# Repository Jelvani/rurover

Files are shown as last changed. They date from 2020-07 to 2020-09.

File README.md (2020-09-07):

# Rutgers Rover (RURover) User Guide (Under Develpoment)

RURover is an unmaned-ground-vehicke (UGV) based on the [Traxxas X-Maxx 8s](https://traxxas.com/products/landing/x-maxx/), that has been modified with the addition of wheel encoders, steering sensor, and an on-board embedded system.

## Hardware
***
A list of all additional hardware added to RURover can be found below:
- Sensors
    - [Wheel encoders (X4)](https://www.usdigital.com/products/encoders/incremental/shaft/S4T)
    - [Steering angle encoder](https://www.usdigital.com/products/encoders/absolute/magnetic/MA3)
    - [Inertial Measurement Unit (IMU)](https://www.adafruit.com/product/2472)
- Embedded System
    - [System on module, NVIDIA Jetson TX2](https://developer.nvidia.com/embedded/jetson-tx2-developer-kit)
    - [Jetson TX2 custom carrier board](https://www.uta.edu/utari/research/robotics/airborne/tutorials.php#TX2version2)
    - [Teensy 4.0 microcontroller](https://www.pjrc.com/store/teensy40.html)
- Batteries
    - [6500 mAh 4s LiPo (X2)](https://www.amazon.com/Youme-Battery-6500mAh-Traxxas-%EF%BC%8CHelicopter%EF%BC%8CAirplane/dp/B07PD2CNQM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)

## Robot Operating System (ROS) Specifications
***

## Connecting to the platform
***
1. Choose the wifi network with SSID `rurover` and password is `rurover-ram-lab`.
2. SSH into the TX2 with `ssh rurover@10.42.0.1` and password is `12`.

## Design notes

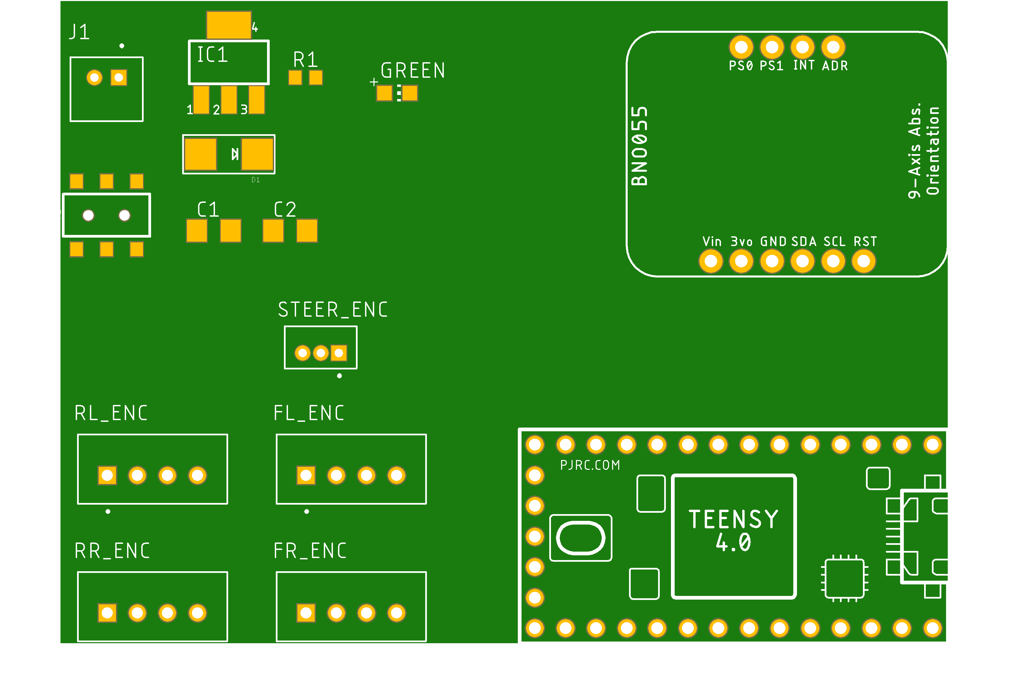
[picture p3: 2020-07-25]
pcb_boards/pcb.png

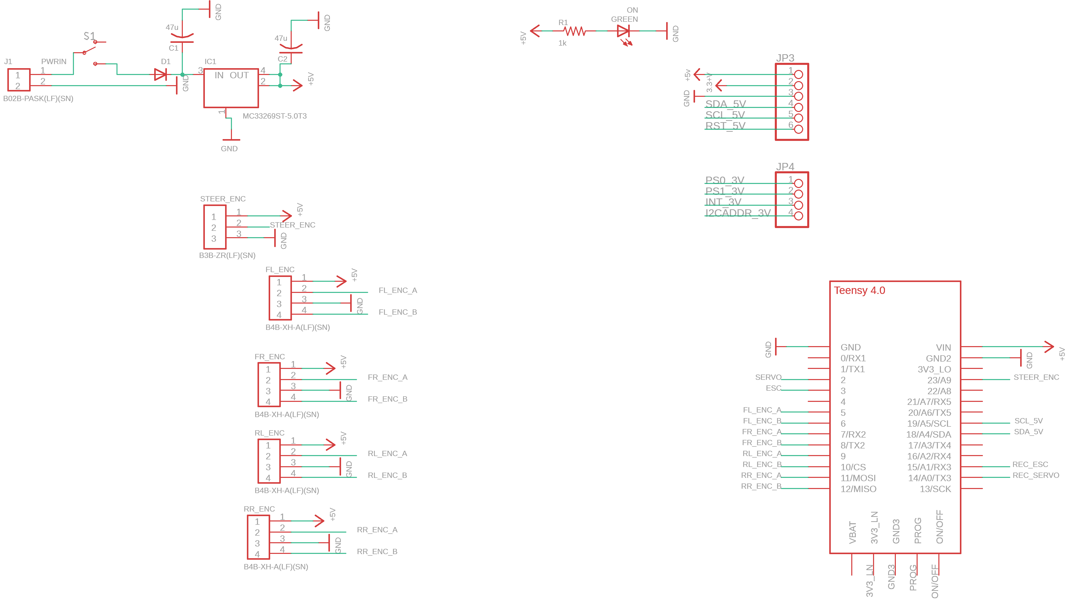
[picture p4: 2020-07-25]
pcb_boards/circuit.png

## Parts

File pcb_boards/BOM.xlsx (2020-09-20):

Part | Value | Device | Package | Description | MF | MPN | MOUNT TYPE
C1 | 0.1uF | C-USC1206 | 1206 | Multilayer Ceramic Capacitors MLCC - SMD/SMT 50V 0.1uF X7R AUTO 5mm Flex VW 80808 | KEMET | C1206X104K5RAC3316 | SMD/SMT
C2 | 10uF | C-USC1206 | 1206 | Multilayer Ceramic Capacitors MLCC - SMD/SMT 16V 10uF Y5V 1206 -20/80% | KEMET | C1206C106Z4VACTU | SMD/SMT
D1 |  | DIODESMA | SMA (DO-214AC) | Schottky Diodes & Rectifiers 40 Volt 1.0 Amp 40 Amp IFSM | Vishay Semiconductors | SS14-E3/5AT | SMD/SMT
ESC |  | JST-XH-02-PIN-LONG-PAD | 2POS | CONN HEADER VERT 2POS 2.5MM | JST Sales America Inc | B2B-XH-A(LF)(SN) | Through Hole
FL_ENC |  | JST-XH-04-PIN-LONG-PAD | 4POS | CONN HEADER VERT 4POS 2.5MM | JST Sales America Inc | B4B-XH-A(LF)(SN) | Through Hole
FR_ENC |  | JST-XH-04-PIN-LONG-PAD | 4POS | CONN HEADER VERT 4POS 2.5MM | JST Sales America Inc | B4B-XH-A(LF)(SN) | Through Hole
GREEN |  | LEDCHIP-LED0805 | 0805 | LED GREEN DIFFUSED 0805 SMD | OSRAM Opto Semiconductors Inc. | LG R971-KN-1 | SMD
IC1 | LM2937IMP-5.0 | LM2937IMP-5.0 | SOT-223-4 | LDO Voltage Regulators 500 MA LDO REG | Texas Instruments | LM2937IMP-5.0/NOPB | SMD
PWR_IN |  | JST-XH-02-PIN-LONG-PAD | 2POS | CONN HEADER VERT 2POS 2.5MM | JST Sales America Inc | B2B-XH-A-M(LF)(SN) | Through Hole
R1 | 1kOhms | R-US_R0603 | 0603 | Thick Film Resistors - SMD AEC-Q200 | Panasonic | ERJ-UP3D1001V | SMD/SMT
RECIEVER |  | JST-XH-03-PIN-LONG-PAD | 3POS | CONN HEADER VERT 3POS 2.5MM | JST Sales America Inc | B3B-XH-A(LF)(SN) | Through Hole
RL_ENC |  | JST-XH-04-PIN-LONG-PAD | 4POS | CONN HEADER VERT 4POS 2.5MM | JST Sales America Inc | B4B-XH-A(LF)(SN) | Through Hole
RR_ENC |  | JST-XH-04-PIN-LONG-PAD | 4POS | CONN HEADER VERT 4POS 2.5MM | JST Sales America Inc | B4B-XH-A(LF)(SN) | Through Hole
S1 |  | SWITCH-SPDT-SMD-AYZ0202 | DPDT | SWITCH SLIDE DPDT 100MA 12V | C&K | AYZ0202AGRLC | SMD
SERVO |  | JST-XH-02-PIN-LONG-PAD | 2POS | CONN HEADER VERT 2POS 2.5MM | JST Sales America Inc | B2B-XH-A(LF)(SN) | Through Hole
STEER_ENC |  | JST-XH-03-PIN-LONG-PAD | 3POS | CONN HEADER VERT 3POS 2.5MM | JST Sales America Inc | B3B-XH-A(LF)(SN) | Through Hole

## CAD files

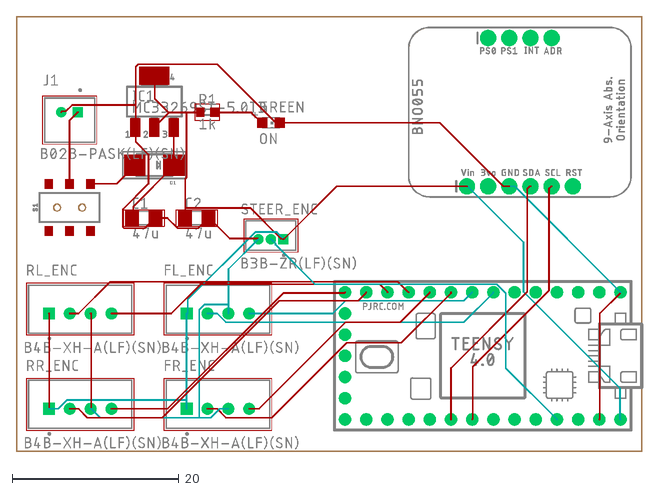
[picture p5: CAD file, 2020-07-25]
pcb_boards/rover.dxf
75.2 x 52.2

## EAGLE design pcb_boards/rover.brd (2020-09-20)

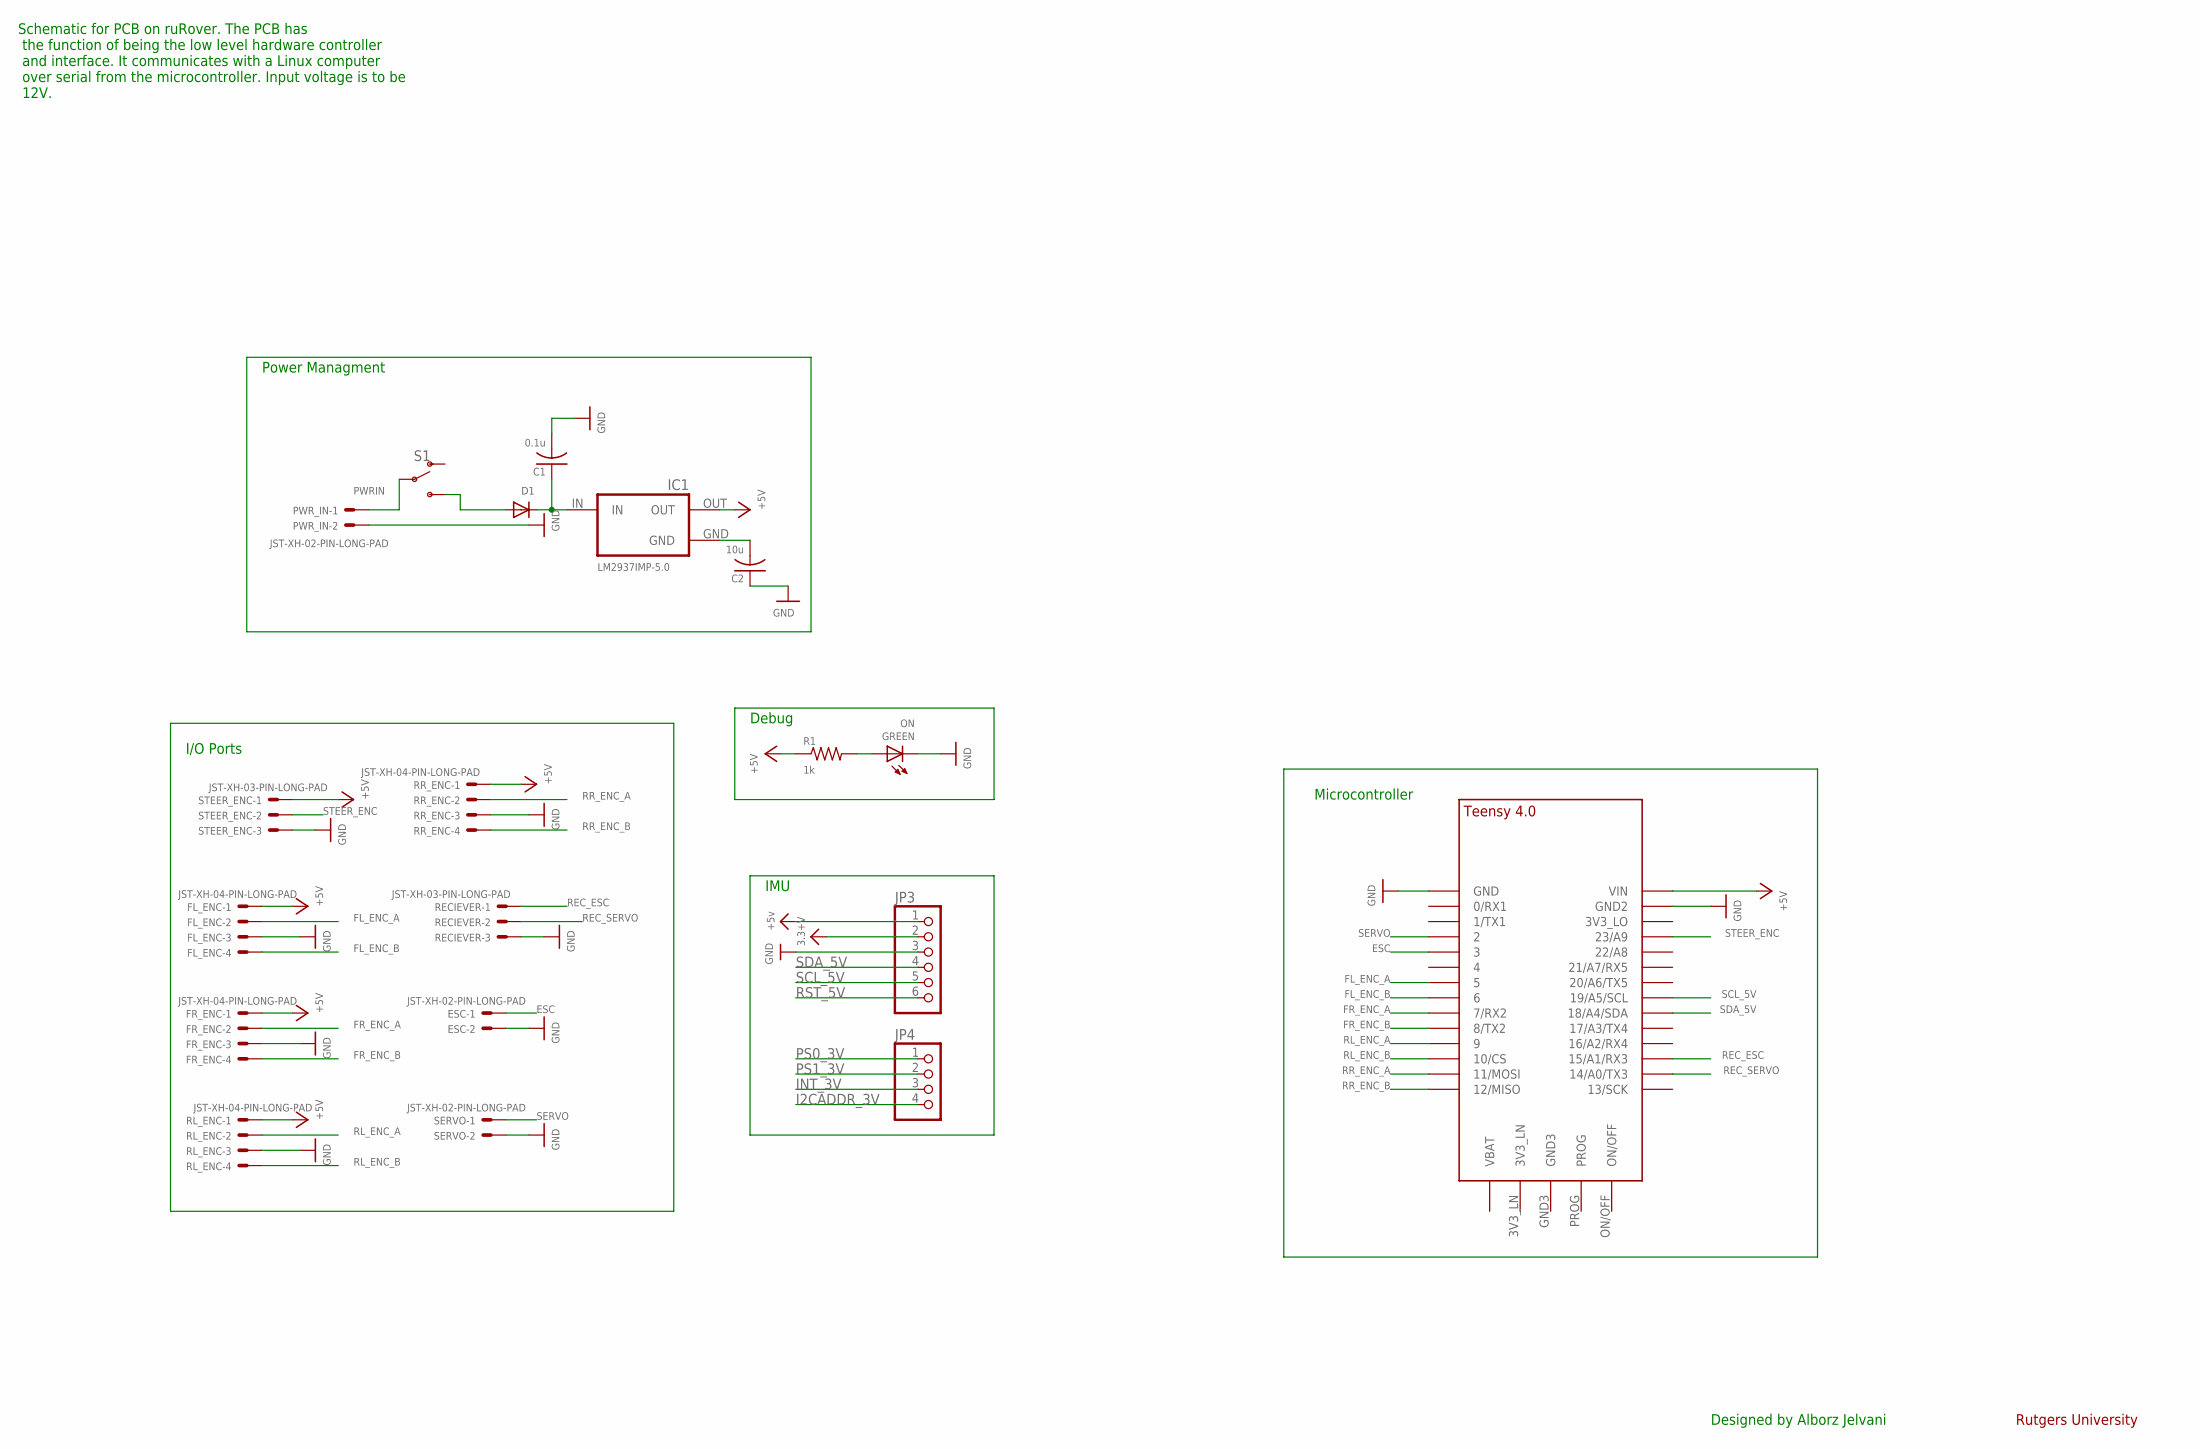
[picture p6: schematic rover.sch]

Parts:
C1: 0.1u; C1206
C2: 10u; C1206
D1: DIODESMA; SMADIODE
ESC: JST-XH-02-PIN-LONG-PAD; JST-XH-02-PACKAGE-LONG-PAD
FL_ENC: JST-XH-04-PIN-LONG-PAD; JST-XH-04-PACKAGE-LONG-PAD
FR_ENC: JST-XH-04-PIN-LONG-PAD; JST-XH-04-PACKAGE-LONG-PAD
GREEN: ON; CHIP-LED0805
IC1: LM2937IMP-5.0; SOT223
JP3: HEADER-1X676MIL; 1X06_ROUND_76
JP4: HEADER-1X476MIL; 1X04_ROUND_76
PWR_IN: JST-XH-02-PIN-LONG-PAD; JST-XH-02-PACKAGE-LONG-PAD
R1: 1k; R0603
RECIEVER: JST-XH-03-PIN-LONG-PAD; JST-XH-03-PACKAGE-LONG-PAD
RL_ENC: JST-XH-04-PIN-LONG-PAD; JST-XH-04-PACKAGE-LONG-PAD
RR_ENC: JST-XH-04-PIN-LONG-PAD; JST-XH-04-PACKAGE-LONG-PAD
S1: SWITCH-SPDT-SMD-AYZ0202; SWITCH_DPDT_SMD_AYZ0202
SERVO: JST-XH-02-PIN-LONG-PAD; JST-XH-02-PACKAGE-LONG-PAD
STEER_ENC: JST-XH-03-PIN-LONG-PAD; JST-XH-03-PACKAGE-LONG-PAD
U$5: TEENSY_4.0-BASIC

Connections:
+3.3V: JP3.2
+5V: FL_ENC.1, FR_ENC.1, IC1.OUT, JP3.1, R1.1, RL_ENC.1, RR_ENC.1, STEER_ENC.1, U$5.VIN
ESC: ESC.1, U$5.3/CANTX (3)
FL_ENC_A: FL_ENC.2, U$5.5
FL_ENC_B: FL_ENC.4, U$5.6
FR_ENC_A: FR_ENC.2, U$5.7 (7/RX2)
FR_ENC_B: FR_ENC.4, U$5.8 (8/TX2)
GND: C1.2, C2.1, ESC.2, FL_ENC.3, FR_ENC.3, GREEN.C, IC1.GND@ (GND), JP3.3, PWR_IN.2, RECIEVER.3, RL_ENC.3, RR_ENC.3, SERVO.2, STEER_ENC.3, U$5.GND, U$5.GND2
I2CADDR_3V: JP4.4
INT_3V: JP4.3
unnamed: GREEN.A, R1.2
unnamed: C1.1, D1.C, IC1.IN
unnamed: D1.A, S1.3 (S)
unnamed: C2.2, IC1.GND
PS0_3V: JP4.1
PS1_3V: JP4.2
PWRIN: PWR_IN.1, S1.2
REC_ESC: RECIEVER.1, U$5.15/A1 (15/A1/RX3)
REC_SERVO: RECIEVER.2, U$5.14/A0 (14/A0/TX3)
RL_ENC_A: RL_ENC.2, U$5.9/CS (9)
RL_ENC_B: RL_ENC.4, U$5.10/CS
RR_ENC_A: RR_ENC.2, U$5.11/MOSI
RR_ENC_B: RR_ENC.4, U$5.12/MISO
RST_5V: JP3.6
SCL_5V: JP3.5, U$5.19/A5/SCL
SDA_5V: JP3.4, U$5.18/A4/SDA
SERVO: SERVO.1, U$5.2
STEER_ENC: STEER_ENC.2, U$5.23/A9

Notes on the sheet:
Rutgers University
Power Managment
I/O Ports
Debug
IMU
Microcontroller
Schematic for PCB on ruRover. The PCB has the function of being the low level hardware controller and interface. It communicates with a Linux computer over serial from the microcontroller. Input voltage is to be 12V.
Designed by Alborz Jelvani

Board: 2 copper layers, 23 parts (0 on the bottom side), 22 nets, no tracks yet.

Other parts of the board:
U$4, U$6, U$7, U$8: 3,6

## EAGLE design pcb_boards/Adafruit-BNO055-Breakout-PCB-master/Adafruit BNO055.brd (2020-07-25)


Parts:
C1, C2: 22pF; 0805-NO
C3: 0.1uF; 0805-NO
C4: 0.1uF; 0805_10MGAP
C5: 10uF; 0805-NO
C6: 10uF; 0805_10MGAP
D1: 1n4148; SOD-323
FID1, FID2: FIDUCIAL""; FIDUCIAL_1MM
JP1: HEADER-1X676MIL; 1X06_ROUND_76
JP2: HEADER-1X476MIL; 1X04_ROUND_76
Q1, Q2: BSS138; SOT23-WIDE
R3, R4, R5, R6, R7, R10: 10K; 0805-NO
R8, R9: 10K; _0805MP
U1: MIC5225-3.3; SOT23-5
U$2: BNO055
U$29, U$30, U$31, U$32: MOUNTINGHOLE2.5_THICK; MOUNTINGHOLE_2.5_PLATED_THICK
Y1: 32.768kHz; CRYSTAL_8X3.8

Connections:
3.3V: C4.2, C6.1, JP1.2, Q1.1 (G), Q2.1 (G), R6.2, R7.2, R10.2, U1.5 (OUT), U$2.3 (VDD), U$2.4 (NBOOT_LOAD_PIN), U$2.28 (VDDIO)
5.0V: C5.1, JP1.1, R8.2, R9.2, U1.1 (IN), U1.3 (EN)
GND: C1.1, C2.1, C3.1, C4.1, C5.2, C6.2, JP1.3, R3.2, R4.2, R5.2, U1.2 (GND), U$2.2 (GND), U$2.10 (PIN10(GND)), U$2.15 (PIN15(GND)), U$2.16 (PIN16(GND)), U$2.18 (COM2(GND)), U$2.25 (GND)
I2CADDR_3V: JP2.4, R5.1, U$2.17 (COM3/I2C_ADDR)
INT_3V: JP2.3, U$2.14 (INT)
unnamed: C1.2, U$2.27 (XIN32), Y1.P$4 (2)
unnamed: C2.2, U$2.26 (XOUT32), Y1.P$1 (1)
unnamed: C3.2, U$2.9 (CAP)
NRESET_3V: D1.A, R10.1, U$2.11 (NRESET)
PS0_3V: JP2.1, R3.1, U$2.6 (PS0)
PS1_3V: JP2.2, R4.1, U$2.5 (PS1)
RST_5V: D1.C, JP1.6
SCL_3V: Q2.2 (S), R7.1, U$2.19 (COM1/SCL/RX)
SCL_5V: JP1.5, Q2.3 (D), R9.1
SDA_3V: Q1.2 (S), R6.1, U$2.20 (COM0/SDA/TX)
SDA_5V: JP1.4, Q1.3 (D), R8.1



Board: 2 copper layers, 26.7 x 20.3 mm, 31 parts (2 on the bottom side), 16 nets.

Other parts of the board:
U$3: PCBFEAT-REV-040
U$28: ADAFRUIT_TEXT_20MM
U$33: ADAFRUIT_2.5MM

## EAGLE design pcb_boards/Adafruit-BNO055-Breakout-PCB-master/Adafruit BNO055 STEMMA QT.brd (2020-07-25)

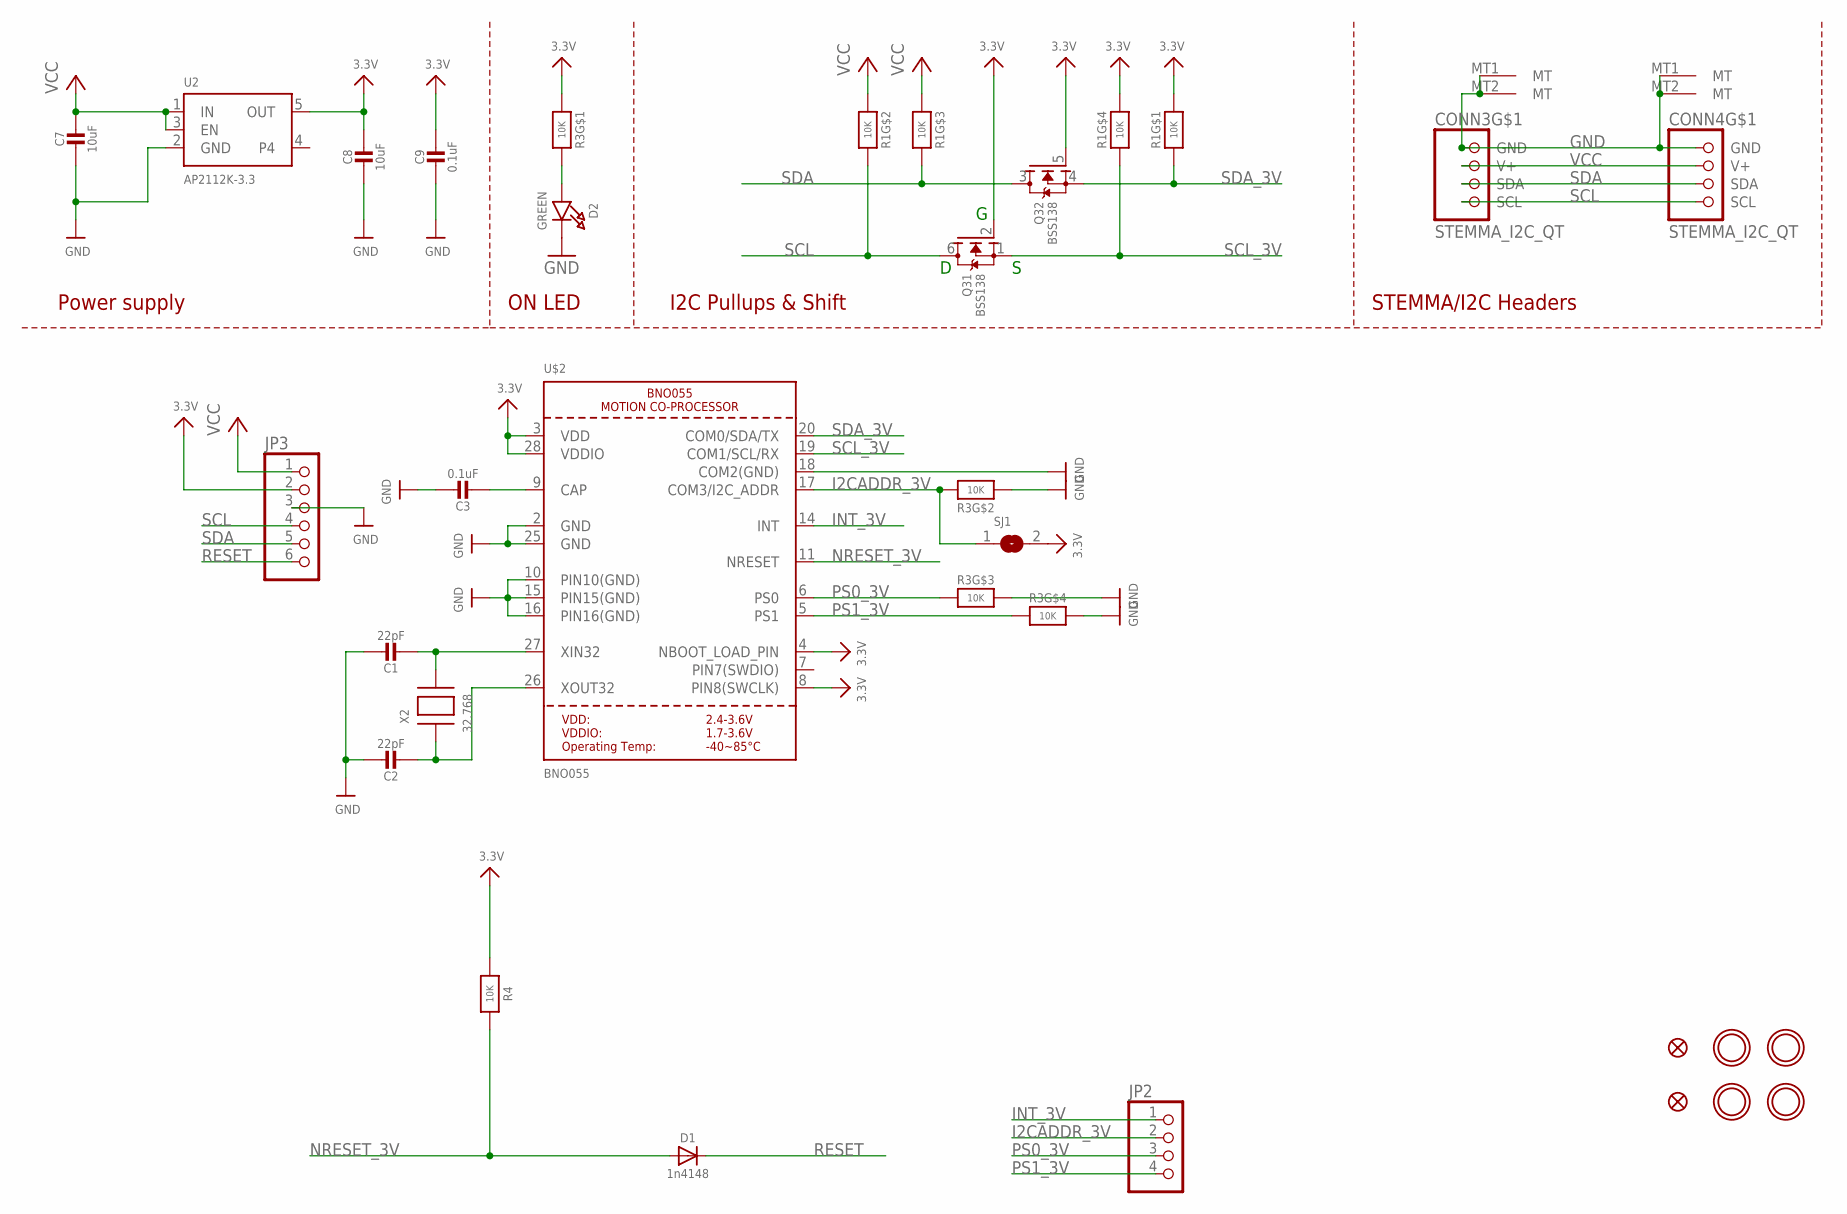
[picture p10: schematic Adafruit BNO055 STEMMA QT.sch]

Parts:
C1, C2: 22pF; 0603-NO
C3, C9: 0.1uF; 0603-NO
C7, C8: 10uF; 0805-NO
CONN3, CONN4: STEMMA_I2C_QT; JST_SH4
D1: 1n4148; SOD-323
D2: GREEN; CHIPLED_0603_NOOUTLINE
FID3, FID4: FIDUCIAL_1MM
JP2: HEADER-1X476MIL; 1X04_ROUND_76
JP3: HEADER-1X670MIL; 1X06_ROUND_70
Q3: BSS138; SOT363
R1, R3: 10K; RESPACK_4X0603
R4: 10K; 0603-NO
SJ1: SOLDERJUMPER; SOLDERJUMPER_ARROW_NOPASTE
U2: AP2112K-3.3; SOT23-5
U$2: BNO055
U$45, U$46, U$48, U$49: MOUNTINGHOLE2.5; MOUNTINGHOLE_2.5_PLATED
X2: 32.768; XTAL3215

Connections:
3.3V: C8.1, C9.1, JP3.2, Q3.2 (G), Q3.5 (G), R1.1, R1.4 (1), R3.1, R4.1, SJ1.2, U2.5 (OUT), U$2.3 (VDD), U$2.4 (NBOOT_LOAD_PIN), U$2.8 (PIN8(SWCLK)), U$2.28 (VDDIO)
GND: C1.1, C2.1, C3.1, C7.2, C8.2, C9.2, CONN3.1 (GND), CONN3.MT1 (MT), CONN3.MT2 (MT), CONN4.1 (GND), CONN4.MT1 (MT), CONN4.MT2 (MT), D2.C, JP3.3, R3.2 (1), R3.5 (2), R3.6 (2), U2.2 (GND), U$2.2 (GND), U$2.10 (PIN10(GND)), U$2.15 (PIN15(GND)), U$2.16 (PIN16(GND)), U$2.18 (COM2(GND)), U$2.25 (GND)
I2CADDR_3V: JP2.2, R3.7 (2), SJ1.1, U$2.17 (COM3/I2C_ADDR)
INT_3V: JP2.1, U$2.14 (INT)
unnamed: C1.2, U$2.27 (XIN32), X2.P$2
unnamed: C2.2, U$2.26 (XOUT32), X2.P$1
unnamed: C3.2, U$2.9 (CAP)
unnamed: D2.A, R3.8 (2)
NRESET_3V: D1.A, R4.2, U$2.11 (NRESET)
PS0_3V: JP2.3, R3.3 (1), U$2.6 (PS0)
PS1_3V: JP2.4, R3.4 (1), U$2.5 (PS1)
RESET: D1.C, JP3.6
SCL: CONN3.4 (SCL), CONN4.4 (SCL), JP3.4, Q3.6 (D), R1.7 (2)
SCL_3V: Q3.1 (S), R1.5 (2), U$2.19 (COM1/SCL/RX)
SDA: CONN3.3 (SDA), CONN4.3 (SDA), JP3.5, Q3.3 (D), R1.6 (2)
SDA_3V: Q3.4 (S), R1.8 (2), U$2.20 (COM0/SDA/TX)
VCC: C7.1, CONN3.2 (V+), CONN4.2 (V+), JP3.1, R1.2 (1), R1.3 (1), U2.1 (IN), U2.3 (EN)

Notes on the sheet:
I2C Pullups & Shift
STEMMA/I2C Headers
ON LED
Power supply

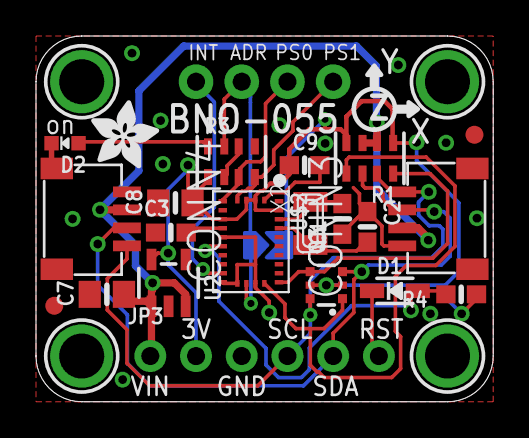
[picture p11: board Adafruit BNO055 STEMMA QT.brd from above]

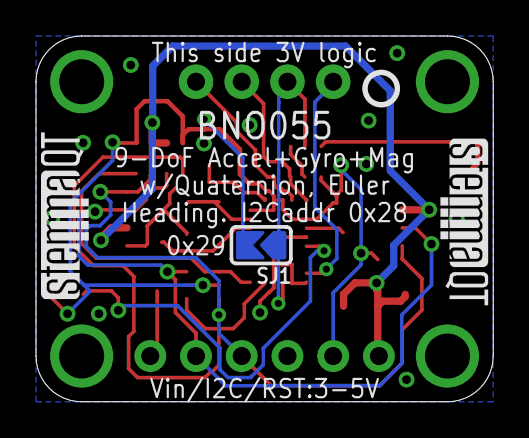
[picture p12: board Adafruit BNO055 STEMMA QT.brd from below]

Board: 2 copper layers, 25.4 x 20.3 mm, 30 parts (4 on the bottom side), 17 nets.

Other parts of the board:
U$51: ADAFRUIT_3.5MM
U$52: PCBFEAT-REV-040
U$53, U$54: STEMMAQT

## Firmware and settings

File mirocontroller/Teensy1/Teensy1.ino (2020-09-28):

#include <ros.h>
#include <std_msgs/Float32.h>
#include <sensor_msgs/Imu.h>
#include <ackermann_msgs/AckermannDriveStamped.h>
#include <std_srvs/SetBool.h>
#include <std_srvs/Empty.h>
#include <Encoder.h>
#include <Wire.h>
#include <Adafruit_Sensor.h>
#include <Servo.h>
#include <Adafruit_BNO055.h>
#include <utility/imumaths.h>
#include "TeensyThreads.h"
#define USE_TEENSY_HW_SERIAL

/****PIN CONNECTION MACROS****/
#define _SERVO 2
#define _ESC 3
#define _FL_A 5
#define _FL_B 6
#define _FR_A 7
#define _FR_B 8
#define _RL_A 9
#define _RL_B 10
#define _RR_A 11
#define _RR_B 12
#define _REC_SERVO 14
#define _REC_ESC 15
#define _STEER 23
/*******Reciever PWM range macros*********/
#define _REC_ESC_MIN 1065
#define _REC_ESC_MAX 2006
#define _REC_SERVO_MIN 1065
#define _REC_SERVO_MAX 2006
#define _ESC_NEUTRAL 1512
#define _SERVO_NEUTRAL 1523


 //TODO add service for switching to computer control


/************STRUCT DEFINTIONS************/
struct ros_message{ //contains all ROS messages
  std_msgs::Float32 flFeedback;
  std_msgs::Float32 frFeedback;
  std_msgs::Float32 rlFeedback;
  std_msgs::Float32 rrFeedback;
  std_msgs::Float32 steeringFeedback;
  std_msgs::Float32 manualSteering;
  std_msgs::Float32 manualThrottle;
  sensor_msgs::Imu imu_dat;
};

struct isr_variables{ //volatile variables changed by ISR's
  volatile unsigned long steering_pwm; //current pwm width in microseconds for steering, 0.351564 degrees per microsecond
  volatile unsigned long reciever_esc_pwm; //current pwm width in microseconds for reciever esc, 1512 neurtral
  volatile unsigned long reciever_servo_pwm; //current pwm width in microseconds for reciever esc, 1523 neurtral
  volatile unsigned long esc_micros;
  volatile unsigned long servo_micros;
  volatile unsigned long steering_micros;
  volatile float steering_angle;
  };

struct steering_calibration_parameters{ //PWM parameters for absolute steering sensor, calculated on startup or on service call
  float MIN_pwm; // typically 476 microseconds, range of PWM is about 112 microseconds
  float MAX_pwm; //typically 581 microseconds
  float MIN_angle;
  float MAX_angle; //typically 37 degrees
};

struct thread_ids{//thread id's to use for killing threads
  int imu;
  int manual_controller;
  int actuator_controller;
  int pid_controller;
  int kinematic_controller;
};
/************ENUM DEFINTIONS************/
enum drive_mode {manual, actuator, pid, kinematic, neutral};
/*********PROTOTYPES**************/
float mapf(float x, float in_min, float in_max, float out_min, float out_max);
void steering_isr();
void rec_servo_isr();
void rec_esc_isr();
void imu_read();
void actuator_controller();
void manual_controller();
void pid_controller();
void kinematic_controller();
void moveCb(const ackermann_msgs::AckermannDriveStamped &msg);
void calibrate_steering(const std_srvs::Empty::Request &req, const std_srvs::Empty::Response &res);
void set_drive_mode(enum drive_mode);
bool switchManualCb(const std_srvs::Empty::Request &req, const std_srvs::Empty::Response &res);
bool switchActuatorCb(const std_srvs::Empty::Request &req, const std_srvs::Empty::Response &res);
bool switchNeutralCb(const std_srvs::Empty::Request &req, const std_srvs::Empty::Response &res);
bool switchPidCb(const std_srvs::Empty::Request &req, const std_srvs::Empty::Response &res);
bool switchKinematicCb(const std_srvs::Empty::Request &req, const std_srvs::Empty::Response &res);
 /************VARIABLES********************/
Encoder fl(_FL_A, _FL_B);
Encoder fr(_FR_A, _FR_B);
Encoder rl(_RL_A, _RL_B);
Encoder rr(_RR_A, _RR_B);
Servo esc;
Servo steer;
ros::NodeHandle nh;

struct ros_message ros_msgs;
struct isr_variables isr_vars;
struct steering_calibration_parameters steering_calab_params;

struct thread_ids t_id;
enum drive_mode mode;//current drive mode variable

ros::Publisher pub_fl_feedback("truck/feedback/wheel/fl", &ros_msgs.flFeedback);
ros::Publisher pub_fr_feedback("truck/feedback/wheel/fr", &ros_msgs.frFeedback);
ros::Publisher pub_rl_feedback("truck/feedback/wheel/rl", &ros_msgs.rlFeedback);
ros::Publisher pub_rr_feedback("truck/feedback/wheel/rr", &ros_msgs.rrFeedback);
ros::Publisher pub_steering_feedback("truck/feedback/steering", &ros_msgs.steeringFeedback);
ros::Publisher pub_manual_steering_command("truck/manual/steering", &ros_msgs.manualSteering);
ros::Publisher pub_manual_throttle_command("truck/manual/throttle", &ros_msgs.manualThrottle);
ros::Publisher pub_imu("truck/imu/data", &ros_msgs.imu_dat);

ros::Subscriber<ackermann_msgs::AckermannDriveStamped> sub_command("truck/in/command", &moveCb); //statically allocated for rosserial using templates


//services for switching drive modes
ros::ServiceServer<std_srvs::Empty::Request, std_srvs::Empty::Response> serv_mode_manual("truck/mode/manual", &switchManualCb);
ros::ServiceServer<std_srvs::Empty::Request, std_srvs::Empty::Response> serv_mode_actuator("truck/mode/actuator", &switchActuatorCb);
ros::ServiceServer<std_srvs::Empty::Request, std_srvs::Empty::Response> serv_mode_kinematic("truck/mode/kinematic", &switchKinematicCb);
ros::ServiceServer<std_srvs::Empty::Request, std_srvs::Empty::Response> serv_mode_pid("truck/mode/pid", &switchPidCb);
ros::ServiceServer<std_srvs::Empty::Request, std_srvs::Empty::Response> serv_mode_neutral("truck/mode/neutral", &switchNeutralCb);
ros::ServiceServer<std_srvs::Empty::Request, std_srvs::Empty::Response> serv_calib_steering("truck/calibrate/steering", &calibrate_steering);

Adafruit_BNO055 bno = Adafruit_BNO055(55,0x28);

volatile sensors_event_t orientationData , angVelocityData , linearAccelData;
/************************************************/


void setup(){

  steering_calab_params.MIN_pwm = 476;
  steering_calab_params.MAX_pwm = 581;
  steering_calab_params.MIN_angle = -37;
  steering_calab_params.MAX_angle = 37;
  
  steer.attach(_SERVO);
  esc.attach(_ESC);
  
  steer.writeMicroseconds(_SERVO_NEUTRAL); //send neutral commands for safety
  esc.writeMicroseconds(_ESC_NEUTRAL);
  
  attachInterrupt(_STEER,steering_isr,CHANGE); //steering encoder pwm
  attachInterrupt(_REC_ESC,rec_esc_isr,CHANGE); //reciever esc pwm
  attachInterrupt(_REC_SERVO,rec_servo_isr,CHANGE); //reciever servo pwm
  
  nh.initNode();
  nh.advertise(pub_fl_feedback);
  nh.advertise(pub_fr_feedback);
  nh.advertise(pub_rl_feedback);
  nh.advertise(pub_rr_feedback);
  nh.advertise(pub_steering_feedback);
  nh.advertise(pub_manual_steering_command);
  nh.advertise(pub_manual_throttle_command);
  nh.advertise(pub_imu);
  nh.subscribe(sub_command);
  nh.advertiseService(serv_mode_manual);
  nh.advertiseService(serv_mode_actuator);
  nh.advertiseService(serv_mode_pid);
  nh.advertiseService(serv_mode_kinematic);
  nh.advertiseService(serv_mode_neutral);
  nh.advertiseService(serv_calib_steering);
  /*****IMU Stuff***********/
  if(bno.begin()){
    delay(1000);//wait for imu
    bno.setExtCrystalUse(true);
    t_id.imu = threads.addThread(imu_read);
    nh.loginfo("Connection to IMU established");
  }else{
    //if not detected, give error and continue
    nh.logerror("IMU not deteced, proceeding without IMU");
  } 
  ros_msgs.imu_dat.header.frame_id = "base_link";
  set_drive_mode(manual);
  //calibrate_steering();
}

unsigned long startMillis; //used for timing of ros rate
unsigned long currentMillis;
int delaytime;
unsigned long steering_pwm_copy;
unsigned long rec_esc_pwm_copy;
unsigned long rec_servo_pwm_copy;

void loop()
{
  startMillis=millis();
  ros_msgs.flFeedback.data = fl.read();
  pub_fl_feedback.publish(&ros_msgs.flFeedback);
  ros_msgs.frFeedback.data = fr.read();
  pub_fr_feedback.publish(&ros_msgs.frFeedback);
  ros_msgs.rlFeedback.data = rl.read();
  pub_rl_feedback.publish(&ros_msgs.rlFeedback);
  ros_msgs.rrFeedback.data = rr.read();
  pub_rr_feedback.publish(&ros_msgs.rrFeedback);

  noInterrupts();//disable interrupts for copying ISR shared variables
  steering_pwm_copy = isr_vars.steering_pwm;
  rec_esc_pwm_copy = isr_vars.reciever_esc_pwm;
  rec_servo_pwm_copy = isr_vars.reciever_servo_pwm;
  interrupts();
  ros_msgs.steeringFeedback.data = mapf(steering_pwm_copy, steering_calab_params.MIN_pwm, steering_calab_params.MAX_pwm, steering_calab_params.MIN_angle, steering_calab_params.MAX_angle); //outputs angle in degrees of steering, center being 0
  ros_msgs.manualSteering.data = mapf(rec_servo_pwm_copy,_REC_SERVO_MIN,_REC_SERVO_MAX,-1,1);//outputs throttle percetange from -1 to 1
  ros_msgs.manualThrottle.data = mapf(rec_esc_pwm_copy,_REC_ESC_MIN,_REC_ESC_MAX,-1,1);
    
  pub_steering_feedback.publish(&ros_msgs.steeringFeedback);
  pub_manual_steering_command.publish(&ros_msgs.manualSteering);
  pub_manual_throttle_command.publish(&ros_msgs.manualThrottle);

  ros_msgs.imu_dat.orientation.x = orientationData.orientation.x;
  ros_msgs.imu_dat.orientation.y = orientationData.orientation.y;
  ros_msgs.imu_dat.orientation.z = orientationData.orientation.z;
  ros_msgs.imu_dat.angular_velocity.x = angVelocityData.gyro.x;
  ros_msgs.imu_dat.angular_velocity.y = angVelocityData.gyro.y;
  ros_msgs.imu_dat.angular_velocity.z = angVelocityData.gyro.z;
  ros_msgs.imu_dat.linear_acceleration.x = linearAccelData.acceleration.x;
  ros_msgs.imu_dat.linear_acceleration.y = linearAccelData.acceleration.y;
  ros_msgs.imu_dat.linear_acceleration.z = linearAccelData.acceleration.z;
  ros_msgs.imu_dat.header.stamp = nh.now();
  pub_imu.publish(&ros_msgs.imu_dat);//slows down serial, comment for debugging
  nh.spinOnce();
  currentMillis=millis();
  currentMillis=currentMillis-startMillis;
  delaytime=10-currentMillis-1;
  if(delaytime<0) delaytime=0;
  delay(delaytime);
}

void moveCb(const ackermann_msgs::AckermannDriveStamped &msg){
  
}

bool switchManualCb(const std_srvs::Empty::Request &req, const std_srvs::Empty::Response &res){//manual rc control mode
  
  set_drive_mode(manual);
  if(mode == manual){
    nh.loginfo("Set drive mode: Manual");
    return true;
  }
  return false;
}

bool switchActuatorCb(const std_srvs::Empty::Request &req, const std_srvs::Empty::Response &res){//raw throttle and steering mode
  set_drive_mode(actuator);
  if(mode == actuator){
    nh.loginfo("Set drive mode: Actuator");
    return true;
  }
  return false;
}

bool switchNeutralCb(const std_srvs::Empty::Request &req, const std_srvs::Empty::Response &res){//neutral mode
  set_drive_mode(neutral);
  if(mode == neutral){
    nh.loginfo("Set drive mode: Neutral");
    return true;
  }
  return false;
}
bool switchPidCb(const std_srvs::Empty::Request &req, const std_srvs::Empty::Response &res){

  set_drive_mode(pid);
  if(mode == pid){
    nh.loginfo("Set drive mode: PID");
    return true;
  }
  return false;
}
bool switchKinematicCb(const std_srvs::Empty::Request &req, const std_srvs::Empty::Response &res){

  set_drive_mode(kinematic);
  if(mode == kinematic){
    nh.loginfo("Set drive mode: Kinematic");
    return true;
  }
  return false;
}

void calibrate_steering(const std_srvs::Empty::Request &req, const std_srvs::Empty::Response &res){
  enum drive_mode prev = mode;
  set_drive_mode(neutral); //nothing else sending commands to esc and servo
  threads.delay(1000);
  nh.loginfo("Steering Calibration in Progress");
  steer.write(0);
  threads.delay(1000);
  noInterrupts();
  steering_calab_params.MIN_pwm = isr_vars.steering_pwm; //get min pwm reading
  interrupts();
  steer.write(180);
  threads.delay(1000);
  noInterrupts();
  steering_calab_params.MAX_pwm = isr_vars.steering_pwm; //get max pwm reading
  interrupts();

  float rangeAngle = abs(steering_calab_params.MIN_pwm - steering_calab_params.MAX_pwm)*0.351564;
  steering_calab_params.MAX_angle = rangeAngle/2;
  steering_calab_params.MIN_angle = -rangeAngle/2;
  set_drive_mode(prev);
  nh.loginfo("Steering Calibration complete");
  }
  
void manual_controller(){
  unsigned long esc_copy;
  unsigned long servo_copy;
  while(1){
    
    noInterrupts();
    servo_copy = isr_vars.reciever_servo_pwm;
    esc_copy = isr_vars.reciever_esc_pwm;
    interrupts();
    steer.writeMicroseconds(servo_copy);
    esc.writeMicroseconds(esc_copy);
    
    threads.delay(10); //100 hz loop
  }
}

void actuator_controller(){
  while(1){
      threads.delay(10); //100 hz loop
  }
}

void pid_controller(){
  while(1){
      threads.delay(10); //100 hz loop
  }
}

void kinematic_controller(){
  while(1){
      threads.delay(10); //100 hz loop
  }
}

void set_drive_mode(enum drive_mode desired_mode){
  switch(mode){
    case manual:
      threads.kill(t_id.manual_controller);
      break;
    case actuator:
      threads.kill(t_id.actuator_controller);
      break;
    case pid:
      threads.kill(t_id.pid_controller);
    case kinematic:
      threads.kill(t_id.kinematic_controller);
    case neutral:
      break;
   }
   
   esc.writeMicroseconds(_ESC_NEUTRAL);
   steer.writeMicroseconds(_SERVO_NEUTRAL);
   
   switch(desired_mode){
    case manual:
      mode = manual;
      t_id.manual_controller = threads.addThread(manual_controller);
      break;
    case actuator:
      mode = actuator;
      t_id.actuator_controller = threads.addThread(actuator_controller);
      break;
    case pid:
      mode = pid;
      t_id.pid_controller = threads.addThread(pid_controller);
      break;
    case kinematic:
      mode = kinematic;
      t_id.kinematic_controller = threads.addThread(kinematic_controller);
      break;
    case neutral:
      mode = neutral;
      break;
   }
}
void imu_read(){
  while(1){
    bno.getEvent(&orientationData, Adafruit_BNO055::VECTOR_EULER);
    bno.getEvent(&angVelocityData, Adafruit_BNO055::VECTOR_GYROSCOPE);
    bno.getEvent(&linearAccelData, Adafruit_BNO055::VECTOR_LINEARACCEL);
    threads.delay(10); //100 hz loop
  }
}
void rec_esc_isr(){
  if(digitalRead(_REC_ESC) == HIGH){
    isr_vars.esc_micros = micros();
  }else{
    if(isr_vars.esc_micros > 0){
      if(micros() > isr_vars.esc_micros && 1000 < (micros() - isr_vars.esc_micros) && 2010 > (micros() - isr_vars.esc_micros)){
        isr_vars.reciever_esc_pwm = micros() - isr_vars.esc_micros;
      }
    }
  }
}

void rec_servo_isr(){
  if(digitalRead(_REC_SERVO) == HIGH){
    isr_vars.servo_micros = micros();
  }else{
    if(isr_vars.servo_micros > 0){
      if(micros() > isr_vars.servo_micros && 1000 < (micros() - isr_vars.servo_micros) && 2010 > (micros() - isr_vars.servo_micros)){
        isr_vars.reciever_servo_pwm = micros() - isr_vars.servo_micros;
      }
    }
  }
}

void steering_isr(){
  if(digitalRead(_STEER) == HIGH){
    isr_vars.steering_micros = micros();
  }else{
    if(isr_vars.steering_micros > 0){
      if(micros() > isr_vars.steering_micros){
        isr_vars.steering_pwm = micros() - isr_vars.steering_micros;
      }
    }
  }
}

float mapf(float x, float in_min, float in_max, float out_min, float out_max)
{
  return (x - in_min) * (out_max - out_min) / (in_max - in_min) + out_min;
}

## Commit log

2020-07-25 added led and power switch
    [rover.sch]
2020-07-25 added design blocks for imu and microcontroller
    [Adafruit BNO055 STEMMA QT.brd, Adafruit BNO055 STEMMA QT.sch, Adafruit BNO055.brd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]
2020-07-27 added esc and servo headers
    [rover.brd, rover.sch]
2020-07-27 added ground planes
    [rover.brd, rover.sch]
2020-07-29 organized schematic
    [rover.sch]
2020-08-10 finished pcb, added BOM
    [Adafruit BNO055 STEMMA QT.brd, Adafruit BNO055 STEMMA QT.sch, Adafruit BNO055.brd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]
2020-08-19 alpha stage for manual control testing and data collection with ROS
2020-08-19 working on fixing esc and servo noise problem
    [Teensy1.ino]
2020-08-21 updated code, fixed interrupt issues
    [Teensy1.ino]
2020-09-06 added drive mode selection, fixed steering calab bug
    [Teensy1.ino]
2020-09-20 changed LDO regulator to active one in stock
    [BOM.xlsx, rover.brd, rover.sch]
2020-09-21 updated disconnet from rosserial issue
    [Teensy1.ino]

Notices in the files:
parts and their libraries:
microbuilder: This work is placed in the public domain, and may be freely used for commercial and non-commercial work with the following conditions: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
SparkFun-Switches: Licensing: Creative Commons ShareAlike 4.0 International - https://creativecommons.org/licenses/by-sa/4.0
